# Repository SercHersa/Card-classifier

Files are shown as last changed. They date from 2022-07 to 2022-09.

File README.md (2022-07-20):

# Card-classifier

En este repositorio, se subirá todo lo referente al desarrollo del proyecto de un clasificador de tarjetas, el cual es un robot movil que llega a un stock de tarjetas y mediante tecnología RFID, detecta dónde deberá llevar la tarjeta y mediante la programación de cirtas trayectorias, la depositará en diferentes estantes.

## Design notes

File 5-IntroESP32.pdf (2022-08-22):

# Introducción a la Ingeniería

## Introducción a Arduino y la placa ESP32

### Objetivo

Familiarizarse con el ambiente de programación de Arduino Aprender a interconectar entradas y salidas a la placa ESP32

### Materiales

Un controlador ESP32 y cable USB para conectarlo a la PC El IDE Arduino con la librería para ESP32
Una tarjeta protoboard,
Tres leds, cables y resistencias

### Introducción

Arduino es probablemente la plataforma de hardware abierto más popular para desarrollo y prototipado rápido de proyectos de sistemas digitales. Ha logrado conformar una amplísima comunidad de desarrolladores que comparten las especificaciones y el código de sus proyectos.

Las tarjetas Arduino tienen una serie de interfaces entrada y salida (E/S) analógicas y digitales que pueden ser programadas para monitorear (con ayuda de sensores) o interactuar (con ayuda de actuadores) con su entorno.

Hay una gran variedad de sensores (por ejemplo, de temperatura, humedad, iluminación, sonido, contaminantes, nutrientes, posicionamiento, velocidad, lector RFID, …) y actuadores (por ejemplo, LEDs, zumbadores, relevadores, acopladores, pinzas, servo motores, …) que pueden conectarse a una placa Arduino a través de sus interfaces programables E/S.

Arduino cuenta con un ambiente de desarrollo integrado (IDE, Integrated Development Environment) para programar las acciones que se desean configurar en la placa. Los programas (llamados sketch) escritos en el IDE se descargan a la placa a través de la interfaz USB.

La popularidad de Arduino es tan grande, que su ambiente de programación se ha vuelto un estándar de facto en la comunidad de hardware abierto. Es por ello que utilizaremos el IDE de Arduino en nuestro primer proyecto.

Si bien las tarjetas Arduino son sumamente populares, no son las únicas. En los últimos años han aparecido muchas otras placas para desarrollo de sistemas digitales por lo que hoy tenemos una amplia gama de opciones.

Entre ellas está el microcontrolador ESP32 de Esspresif Systems, un dispositivo sumamente poderoso y versátil. Al igual que las placas Arduino, puede recibir y enviar datos analógicos y digitales, procesar datos e interactuar con usuarios a través de la computadora personal. Además, el módulo ESP32 tiene integrado un chip Bluetooth y uno WiFi lo que le permite conectarse a Internet.

En nuestro primer proyecto, el Robot que utilizará está controlado por una tarjeta Arduino y el lector RFID, que programará usted, está controlado por una tarjeta ESP32.

## Desarrollo

### 1. Instalación del IDE y de las librerías

El IDE permite expresar un programa (un sketch) en un lenguaje muy parecido a C que se compila en el lenguaje de máquina del micro-controlador de la placa. Descargue el IDE de la siguiente dirección: https://www.arduino.cc/en/Main/Software.

Para poder programar el módulo ESP32 desde el IDE de Arduino, es necesario configurar el IDE y cargar algunas librerías. Para ello, sigas las instrucciones en esta liga: https://randomnerdtutorials.com/installing-the-esp32-board-in-arduino-ide-windows-instructions/. NO SE DESESPERE. ESTO TOMARÁ ALGÚN TIEMPO. (Nota: No es necesario que (https://randomnerdtutorials.com/installing-the-esp32-board-in-arduino-ide-windows-instructions/) haga la validación buscando redes WiFi).

### 2. Verificación

Como se señala en la guía anterior, una vez configurado el IDE, deberá seleccionar la placa ESP32 y el puerto COM en la que está conectada. La placa que se le entregó para este proyecto es DOIT

ESP DEVKIT V1 .

1. Conecte el módulo a su PC a través del cable USB. Se debió haber encendido un led rojo indicando que la placa está energizada.
2. En el IDE de Arduino, en el menú Herramientas , seleccione la placa

ESP32 Arduino/DOIT ESP DEVKIT V1
3. En el mismo menú seleccione el puerto al que está conectada la placa
4. En el menú Archivo/Ejemplos/ seleccione el sketch 01.Basics/Blink
5. Compílelo dando clic en el ícono con una paloma. Si no tiene errores, cárguelo a la placa dando clic en la flecha a la derecha:

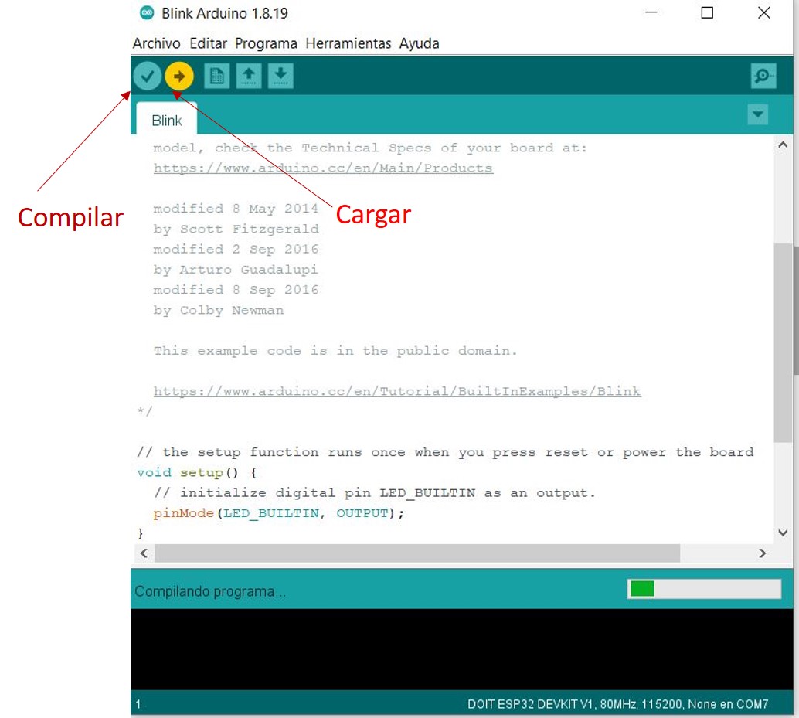
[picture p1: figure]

Figura 1. Compilar y cargar un sketch en el IDE de Arduino

6. Si todo está correcto, podrá ver un led azul parpadeando

EJERCICIO 1. ( 1 Punto). Muestre el led parpadeando al profesor

7. Ahora modifique el sketch para que el led se mantenga encendido un segundo y apagado medio segundo.

EJERCICIO 2. (2 Puntos). Muestre al profesor el led parpadeando con las modificaciones solicitadas

EJERCICIO 3. (1 Punto). Analice y describa brevemente qué hace el código.

### 3. Conectar y manipular un led externo

En esta sección nos vamos a familiarizar con la conexión de componentes electrónicos en una tarjeta protoboard, (también conocidas como Breadboard) como la mostrada en la Figura 2:

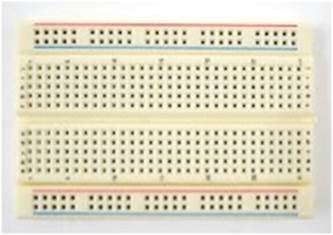
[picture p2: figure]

Figura 2. Tarjeta Protoboard

Las tarjetas protoboard (placa de pruebas) permiten crear rápidamente prototipos de circuitos electrónicos. Son tablas con orificios que se encuentran interconectados entre sí internamente. En la Figura 2, los orificios paralelos a las líneas rojas y azules están interconectados y se usan típicamente para transportar señales de voltaje y de tierra. Los orificios verticales (las columnas) entre las muescas de la tarjeta (por ejemplo, los orificios 12A a 12E), también están interconectados entre sí.

Vamos a colocar un LED en la tarjeta protoboard que encenderemos y apagaremos desde el ESP32. Para ello, el "cátodo" del LED, que se reconoce por ser la pata más corta y tener una muesca plana en el plástico que lo recubre, se conecta a tierra. El "anodo" se conecta a una pata digital de Entrada/Salida (E/S) de la placa ESP32 a través de un resistor de 1kOhm (en realidad, el valor no importa demasiado; resistencias más grandes,disminuirán la corriente y con ello, la intensidad de luminosidad del led).

Existen muchos modelos ESP32. El que se le entregó tiene 30 pines. La distribución de pines en ese modelo es la que se muestra en la figura 3:

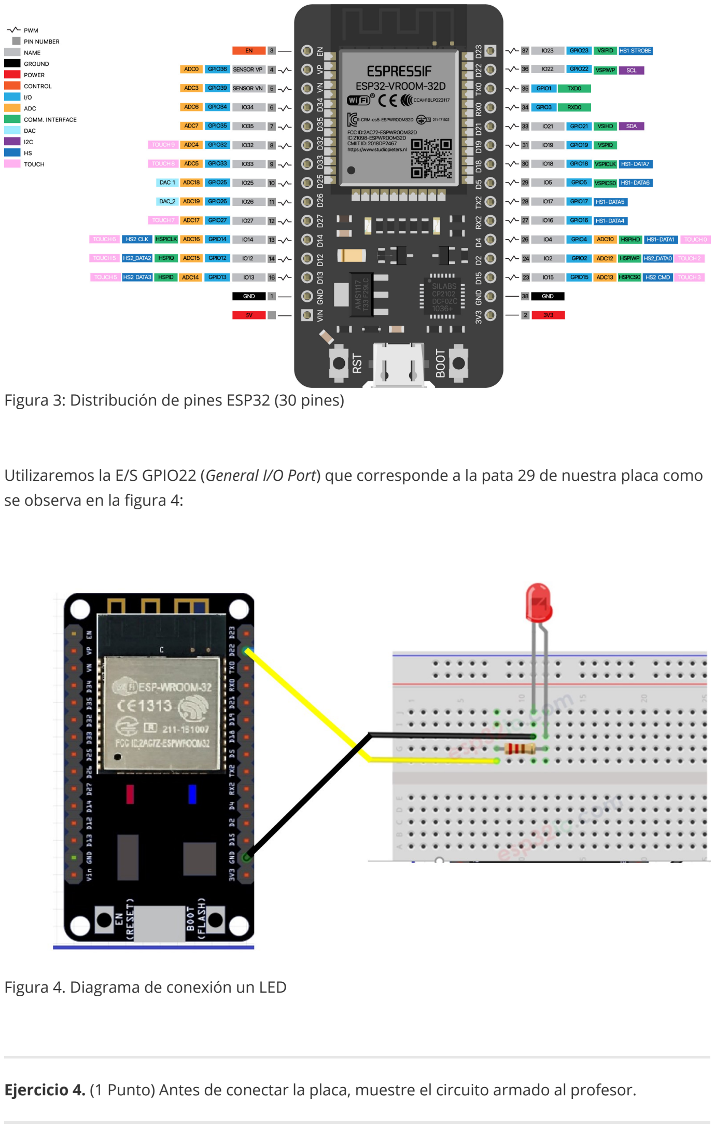
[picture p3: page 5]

Figura 3: Distribución de pines ESP32 (30 pines)

Utilizaremos la E/S GPIO22 (General I/O Port) que corresponde a la pata 29 de nuestra placa como se observa en la figura 4:

Figura 4. Diagrama de conexión un LED

Ejercicio 4. (1 Punto) Antes de conectar la placa, muestre el circuito armado al profesor.

Guarde el código del sketch de parpadeo con un nuevo nombre, por ejemplo, "LedExterno". Vamos a modificar el código para que cuando el LED de la placa esté encendido, el LED en el protoboard se apague y viceversa. Los segmentos de código que necesitará son los siguientes:

EJERICIO5. (2 Puntos). Modifique el código, cárguelo a la placa ESP32 y muestre el circuito funcionando al profesor.

EJERICIO 6. (3 Puntos). Muy bien. Ahora deberá conectar dos LEDs adicionales en los pines de E/S que usted desee. No se olvide de conectar los LEDs con resistores a los pines. Escriba un sketch para que los tres LEDS se alternen en el encendido: LED1 un segundo, LED2 un segundo, LED3 un segundo.

Muestre el sistema funcionando a su profesor

// Antes de setup
#define LED_PROTOBOARD 22 // GPIO que se utilizará para iluminar LED externo

// En setup
pinMode(LED_PROTOBOARD, OUTPUT); // GPIO22 como salida digital

// En loop
digitalWrite(LED_PROTOBOARD, HIGH); ...
digitalWrite(LED_PROTOBOARD, LOW); ...

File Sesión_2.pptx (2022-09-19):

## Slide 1

Clasificador de
tarjetas

M.I. Sergio Hernández Sánchez
sergio.hernandez.sanchez@itam.mx

1

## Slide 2

Salidas Digitales

M.I. Sergio Hernández Sánchez

2

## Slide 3

ESP32 DEVKIT v1 - PINOUT

GPIO = General Purpose Input/Output

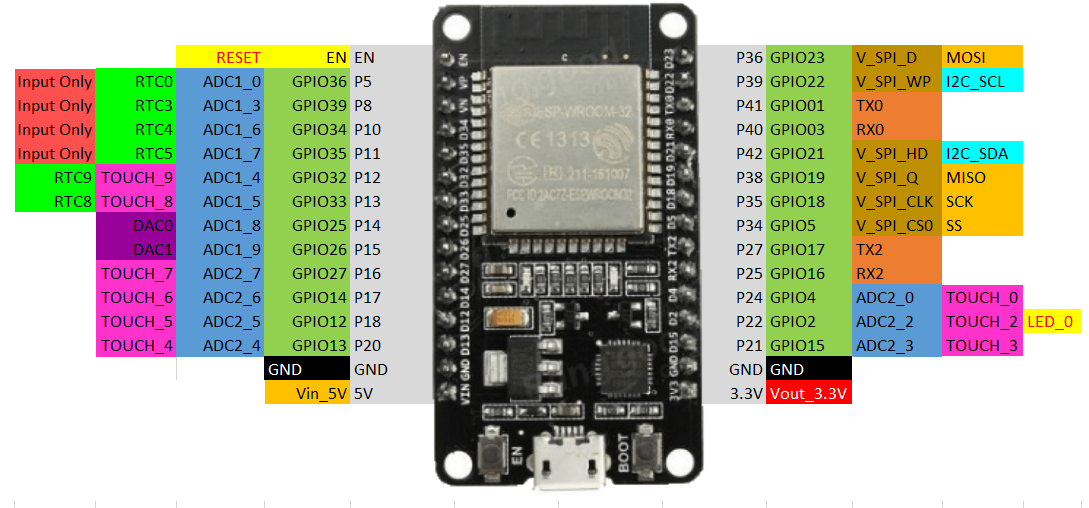
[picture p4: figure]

M.I. Sergio Hernández Sánchez

3

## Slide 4

Salidas digitales

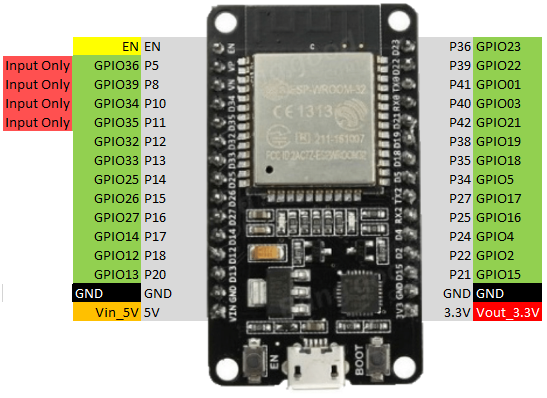
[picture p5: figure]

M.I. Sergio Hernández Sánchez

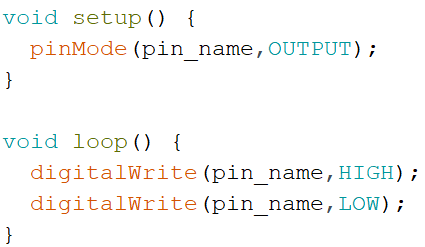
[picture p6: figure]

4

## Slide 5

Comunicación Serial

M.I. Sergio Hernández Sánchez

5

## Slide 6

Comunicación Serial

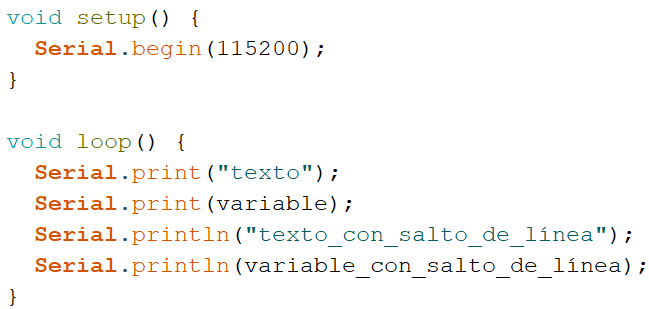
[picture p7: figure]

M.I. Sergio Hernández Sánchez

6

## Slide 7

Entradas digitales

M.I. Sergio Hernández Sánchez

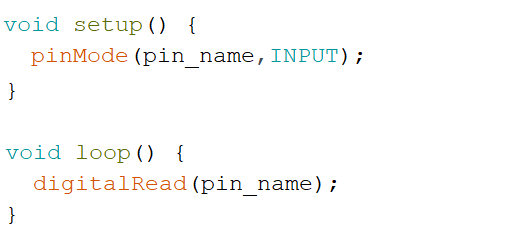
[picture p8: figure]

7

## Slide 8

Entradas digitales

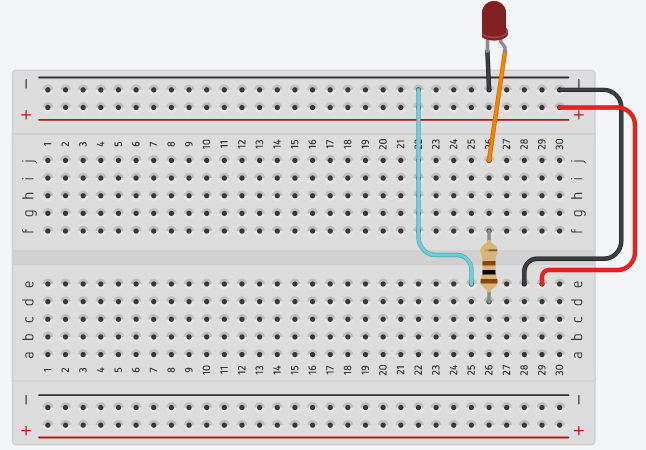
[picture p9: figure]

M.I. Sergio Hernández Sánchez

8

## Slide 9

Entradas digitales

M.I. Sergio Hernández Sánchez

9

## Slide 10

Entradas digitales

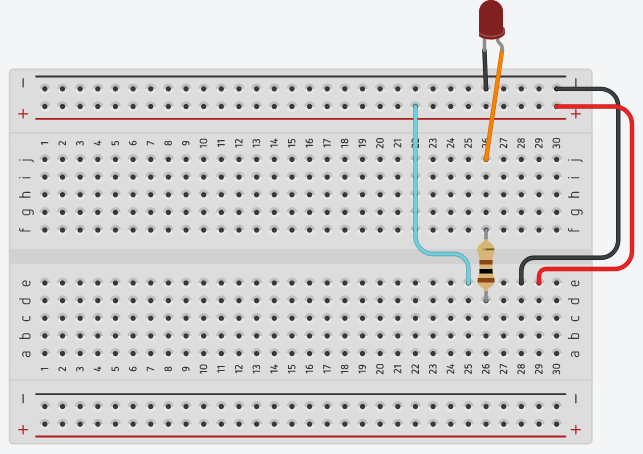
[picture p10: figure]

M.I. Sergio Hernández Sánchez

10

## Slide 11

Entradas digitales

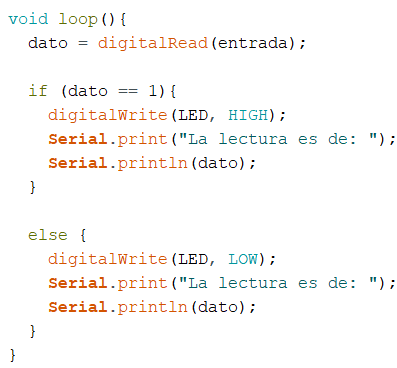
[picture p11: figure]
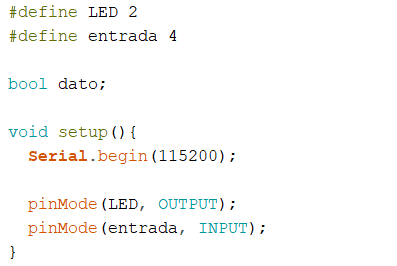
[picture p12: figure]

M.I. Sergio Hernández Sánchez

11

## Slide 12

Funciones

M.I. Sergio Hernández Sánchez

12

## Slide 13

Funciones

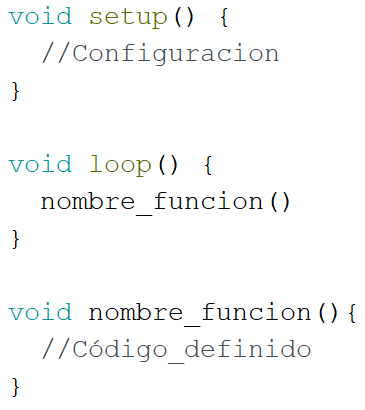
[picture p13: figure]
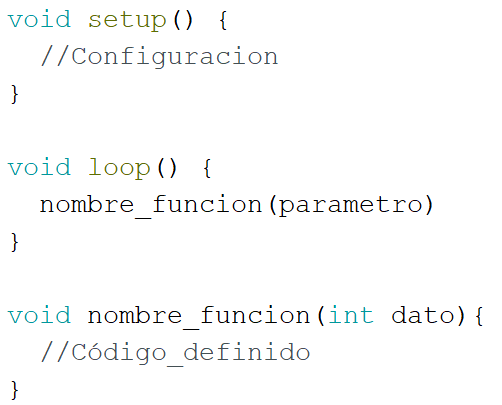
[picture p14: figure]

M.I. Sergio Hernández Sánchez

13

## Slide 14

Codificador binario

M.I. Sergio Hernández Sánchez

14

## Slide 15

Circuito codificación

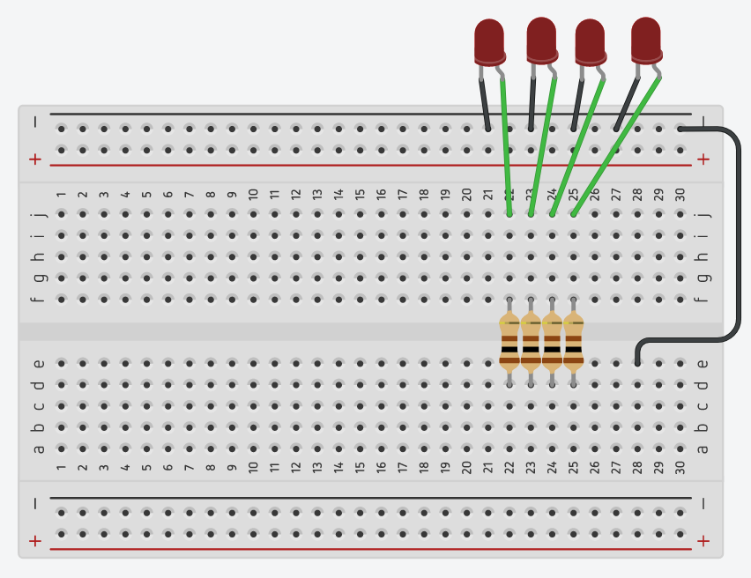
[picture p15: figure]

M.I. Sergio Hernández Sánchez

15

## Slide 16

Reto

Hacer un contador binario de 0 a 15, incrementando la cuenta de uno en uno cada segundo y se reinicie para volver a hacer la cuenta. Este incremento se debe mostrar con cuatro leds y a su vez, mostrarse en el monitor serial.

M.I. Sergio Hernández Sánchez

16

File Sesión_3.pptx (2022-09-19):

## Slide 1

Clasificador de
tarjetas

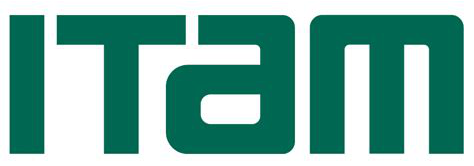
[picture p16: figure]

M.I. Sergio Hernández Sánchez
sergio.hernandez.sanchez@itam.mx

1

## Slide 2

Lector RFID

M.I. Sergio Hernández Sánchez

2

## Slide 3

Lector RFID

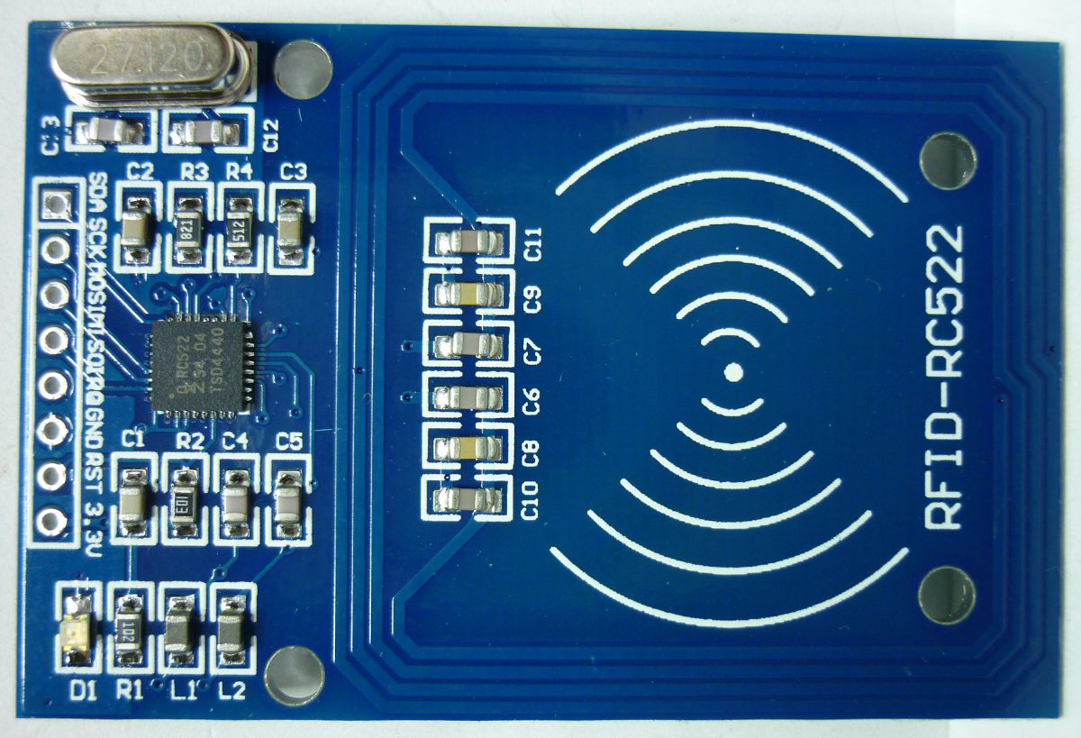
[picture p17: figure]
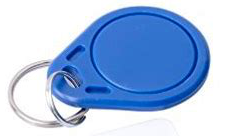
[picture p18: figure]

M.I. Sergio Hernández Sánchez

3

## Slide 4

Conexión

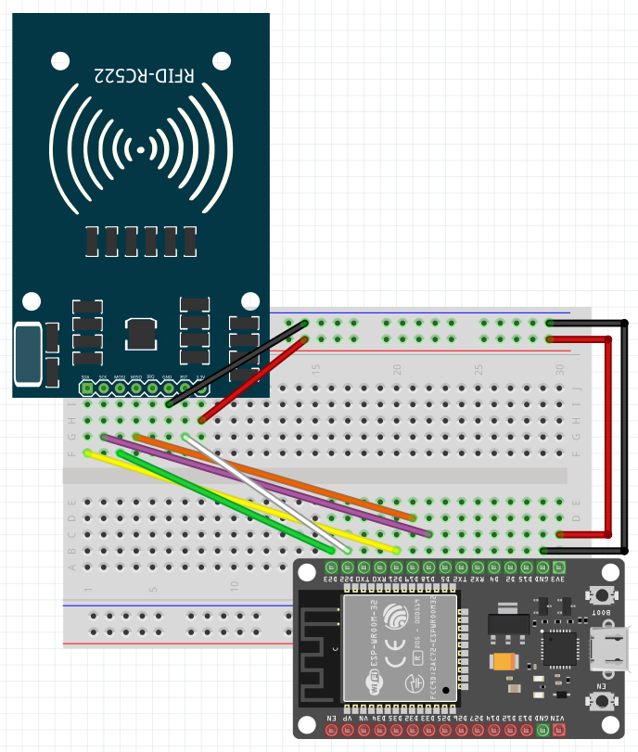
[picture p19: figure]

M.I. Sergio Hernández Sánchez

4

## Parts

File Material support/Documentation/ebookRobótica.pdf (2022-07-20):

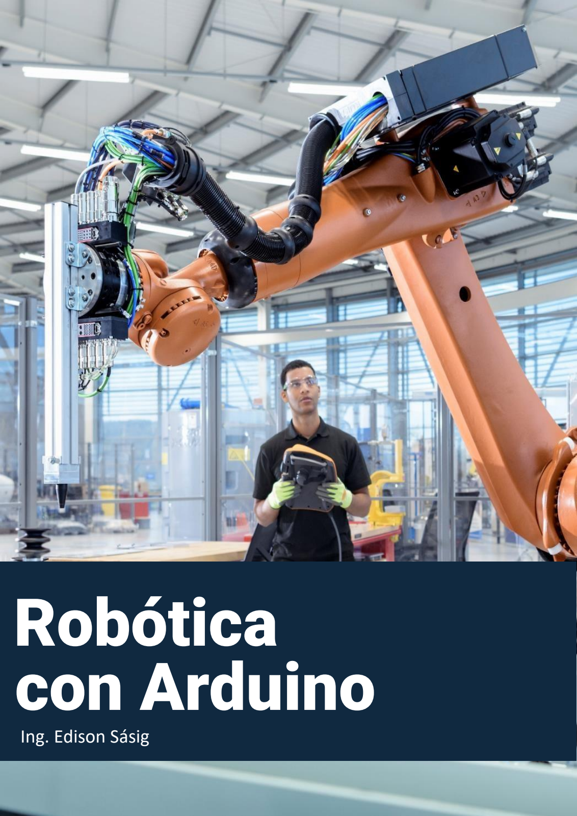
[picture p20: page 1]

# Ing. Edison Sásig

# Robótica con Arduino

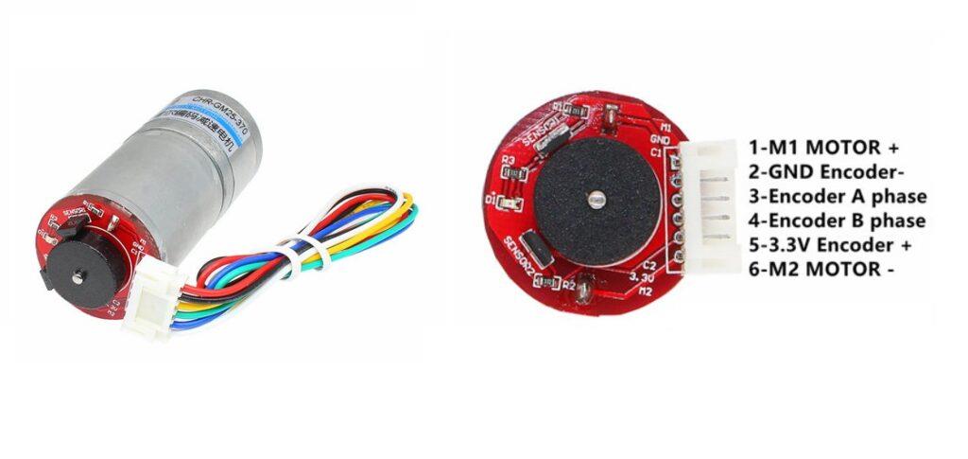
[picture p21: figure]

1 | Ing. Edison Sásig

# Encoder de cuadratura para Robótica

# ¿Qué es un encoder de cuadratura?

Un encoder de cuadratura es un tipo de encoder rotativo incremental que tiene la capacidad de indicar tanto la posición como la velocidad y la dirección del movimiento del eje del motor.

En este apartado vamos a revisar encoders con sensores magnéticos de efecto Hall. A diferencia de los encoders ópticos, los sensores hall al ser magnéticos pueden trabajar en entornos extremos (temperatura, salpicadura de fluidos, grasas, etc) y polvorientos; no hará falta mantenimiento de limpieza.

Debido a estas características los encoder en cuadratura son muy útiles para las siguientes aplicaciones en robótica:

- Robots móviles tipo Uniciclo
- Robots móviles tipo omnidireccional (Mecanum, 3 ruedas)
- Robots móviles tipo Car-Like
- Brazos robóticos
- Robot tipo péndulo
- Robot rueda esférica y mucho más.

Este encoder tiene dos sensores de efecto Hall que generan dos señales de pulsos digitales desfasada en 90º eléctricos o en cuadratura gracias a un disco magnético giratorio, montado en el eje trasero del motor. A estas señales de salida, se les llama comúnmente A y B. Estos dos sensores se van activando y desactivando en una secuencia que nos permite saber la dirección y el número de desplazamientos que han ocurrido en el encoder.

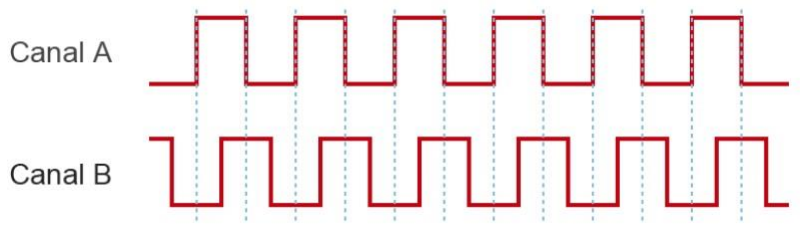
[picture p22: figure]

# Sentido de giro

Para la determinar el sentido de giro (signo), se toman como referencia el desfasamiento que existe entre las señales AB. El hecho de trabajar con dos canales, nos lleva a tener 4 estados, estos mismos son la combinación de A y B.

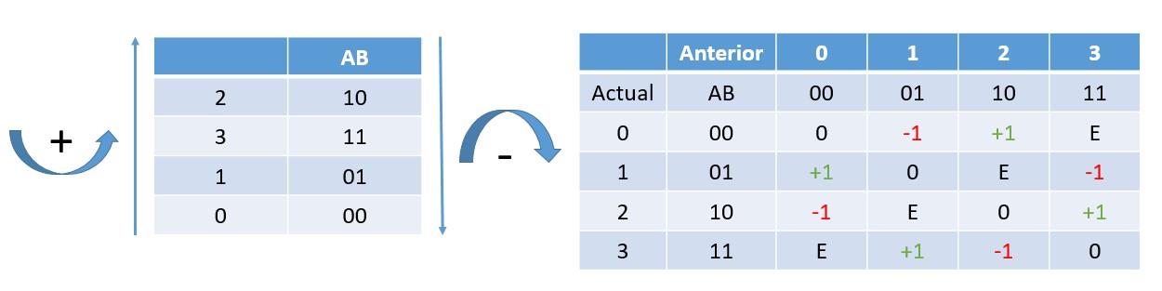
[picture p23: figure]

Si asumimos la salida A como el bit más significativo y la salida B como el bit menos significativo, en la tabla de verdad podemos saber la dirección de giro, si comparamos el estado actual con el estado anterior.

Además, en la figura también se muestra una matriz de incrementos donde podemos comparar el estado anterior con el actual y saber cómo fue el movimiento. Por ejemplo, si el estado anterior fue 01 y el estado actual del encoder es 11 podemos saber que el motor está girando en sentido anti-horario (+). Esta matriz es muy útil para saber en pocos pasos que ocurre con el encoder. También nos puede servir para detectar errores de nuestra señal o del encoder. Ya que hay 4 combinaciones que no pueden aparecer en nuestra señal, como por ejemplo la combinación (11,00), marcada con una E en la matriz.

# Resolución

La resolución de un encoder es una medida en pulsos por revolución (PPR), es decir el número de conteo (cuentas) que genera el encoder en cada vuelta. En el caso de los motores Chihai Motor CHR-GM25-370 de 140RPM a 12v, el encoder incremental de cuadratura emite 11 cuentas por revolución del eje del motor, que corresponde a 495 cuentas por revolución del eje de salida de la caja de reductora (Holzer resolution).

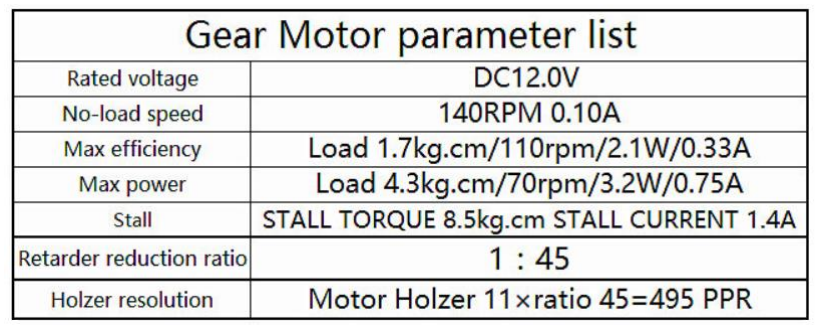
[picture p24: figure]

Respecto a la precisión, tenemos más de una opción.

- Precisión simple, registrando un único flanco (subida o bajada) en un único canal.
- Precisión doble, registrando ambos flancos en un único canal.
- Precisión cuádruple, registrando ambos flancos en ambos canales.

# Resolución para una precisión cuádruple

Para aplicaciones de robótica se utiliza la precisión cuádruple, esta precisión es la que permite detectar el sentido de giro del eje del motor. Por lo tanto, la resolución del encoder para una precisión cuádruple (R) se calcula de manera diferente al Holzer resolution.

# R mH s r = × ×

Donde:

R :
Es la resolución del encoder para una precisión cuádruple.

mH :
Es el número de cuentas por revolución del eje del motor (Motor Holzer). En nuestro

caso 11.

s:
Es el número de estados generado por los canales AB. En nuestro caso 4.

r:
Es la relación de reducción de la caja reductora (ratio). En nuestro caso 45 cuentas por

revolución.

Por lo tanto,
R = | × × | = 11 4 45 1980

# Sentido de giro en Arduino

En base a la tabla anterior se debe crear un código que permita comparar el estado anterior y el estado actual de los pines C1 (canal A) y C2 (canal B) del encoder.

En primer lugar, se debe detectar los flancos de subida y bajada de ambos canales AB. Para esta tarea lo más recomendable es usar interrupciones. Entonces, definimos los pines y las variables que se van a utilizar, configuramos los pines como entradas y activamos las interrupciones para detectar ambos flancos.

const int | C1 = 3; | // Entrada de la señal A del encoder.
const int | C2 = 2; | // Entrada de la señal B del encoder.

void setup()
{

pinMode(C1, INPUT);
pinMode(C2, INPUT);

attachInterrupt(digitalPinToInterrupt(C1), encoder, CHANGE); attachInterrupt(digitalPinToInterrupt(C2), encoder, CHANGE);

}

En la función encoder vamos a comparar el estado anterior y actual e incrementar o decrementar un contador según la tabla. Para esta tarea, vamos a leer un puerto completo que dependiendo en donde se encuentre conectado los pines puede variar.

Los chips utilizados en la placa Arduino (ATmega8 y ATmega168) tienen tres puertos:

- B (pines digitales de 8 a 13) PINB
- C (pines de entrada analógica) PINC
- D (pines digitales de 0 a 7) PIND

En este caso estamos utilizando los pines 2 y 3 es decir el puerto D, por lo tanto, para leer el puerto completo usaremos PIND.

Adicionalmente, debemos filtrar solo los pines de interés este caso el 2 y 3. Entonces considerando que los puertos de Arduino (ATmega8 y ATmega168) son de 8 bits se puede aplicar una operación and entre el valor de PIND y 00001100 (12 DECIMAL).

Entonces en base a tabla debemos hacer la comparación sin olvidar que los valores de la tabla también cambian en base a la conexión de los pines, es decir, si hay un flanco en el canal A (pin 3) y nada en el canal B (pin 2) el valor binario es 10 (2 DECIMAL) se debe cambiar a 00001000 (8 DECIMAL) y así en todas las combinaciones 00, 01 y 11.

0 0 0 0 | 1 1 | 0 0
7 6 5 4 | 3 2 | 1 0
0 0 0 0 | 1 0 | 0 0
7 6 5 4 | 3 2 | 1 0

// Encoder precisión cuádruple. void encoder(void)
{

ant=act;
act=PIND & 12;
if(ant==0 | && act== 4) | n++;
if(ant==4 | && act==12) | n++;
if(ant==8 | && act== 0) | n++;
if(ant==12 && act== 8) | n++;
if(ant==0 && act==8) | n--;
if(ant==4 && act==0) | n--;
if(ant==8 && act==12) n--; if(ant==12 && act==4) n--;

}

Entonces, si cargamos el siguiente sketch en Arduino al dar una vuelta completa al eje del motor se debe mostrar en el monitor serial el valor de la resolución del encoder para una precisión cuádruple

R
. Para este caso

R =1980 .

const int | C1 = 3; | // Entrada de la señal A del encoder.
const int | C2 = 2; | // Entrada de la señal B del encoder.

volatile int n = 0;
volatile byte ant | = 0;
volatile byte act | = 0;
unsigned long lastTime = 0; | // Tiempo anterior
unsigned long sampleTime = 100; | // Tiempo de muestreo

void setup()
{
Serial.begin(9600);

pinMode(C1, INPUT);
pinMode(C2, INPUT);

attachInterrupt(digitalPinToInterrupt(C1), encoder, CHANGE); attachInterrupt(digitalPinToInterrupt(C2), encoder, CHANGE);

Serial.println("Numero de conteos");

}

void loop() {
if (millis() - lastTime >= sampleTime)
{ // Se actualiza cada sampleTime (milisegundos) lastTime = millis();
Serial.print("Count: ");Serial.println(n); }
}

// Encoder precisión cuádruple. void encoder(void)
{

ant=act;
act=PIND & 12;
if(ant==0 | && act== 4) | n++;
if(ant==4 | && act==12) | n++;
if(ant==8 | && act== 0) | n++;
if(ant==12 && act== 8) | n++;
if(ant==0 && act==8) | n--;
if(ant==4 && act==0) | n--;
if(ant==8 && act==12) n--; if(ant==12 && act==4) n--;

}

El código anterior se aplica para un solo motor. Sin embargo, en robótica el número de motores puede ser mucho mayor dependiendo de la aplicación. Entonces vamos a necesitar pines adicionales con interrupciones, y como saben Arduino (ATmega8 y ATmega168) dispone de dos interrupciones externas, por lo cual debemos usar otro Arduino como el MEGA o incluso un ESP32 que tienes muchas características adicionales al tradicional Arduino.

Sin embargo, el Arduino tradicional dispone de interrupciones especiales llamadas PINCHANGE INTERRUPTIONS, las cuales se pueden utilizar en todos los pines incluso en las entradas analógicas, pero son un poco complejas de administrar, sin embargo, gracias la librería PinChangeInterrupt.h podemos utilizar estas interrupciones de la misma manera que una interrupción normal.

En el siguiente ejemplo se ha empleado las interrupciones en el puerto C y en los pines A4 (canal A) y A5 (canal B).

#include "PinChangeInterrupt.h"

const int C1 = A5;
const int C2 = A4;
volatile int n = 0;
volatile int ant | = 0;
volatile int act | = 0;

unsigned long lastTime, sampleTime = 100;

void setup() {

Serial.begin(9600);

pinMode(C1, INPUT);
pinMode(C2, INPUT);

attachPinChangeInterrupt(digitalPinToPinChangeInterrupt(C1), encoder, CHANGE);
attachPinChangeInterrupt(digitalPinToPinChangeInterrupt(C2), encoder, CHANGE);

lastTime = millis();

}

void loop() {
if(millis()-lastTime >= sampleTime) {
lastTime = millis();
Serial.println(n);
}
}

void encoder(void)
{

ant=act;
act=PINC & 48;
if(ant==0 | && act==16) | n++;
if(ant==16 && act==48) | n++;
if(ant==32 && act== 0) | n++;
if(ant==48 && act==32) | n++;
if(ant==0 | && act==32) | n--;
if(ant==16 && act== 0) | n--;
if(ant==32 && act==48) | n--;
if(ant==48 && act==16) | n--;

}

Recuerda que para leer todo el puerto C se debe usar PINC y también se debe realizar la conversión en decimal de los estados de los pines A4 y A5.

# Posición en grados

Para medir la posición relativa del eje del motor, vamos a utilizar la siguiente fórmula.

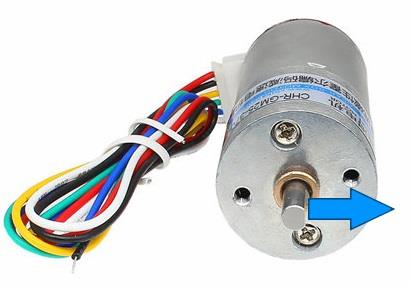
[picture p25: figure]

8 | Ing. Edison Sásig n 360 P
R

×
=

Donde:

P :
Es la posición relativa en grados.

n :
Es el número de cuentas generadas.

R :
Es la resolución del encoder para una precisión cuádruple. En nuestro caso 1980

cuentas por revolución.

# Posición en grados en Arduino

Una vez verificado el código anterior es muy fácil obtener la posición, velocidad y sentido de giro del eje del motor, simplemente hay que aplicar las fórmulas.

const int | C1 = 3; | // Entrada de la señal A del encoder.
const int | C2 = 2; | // Entrada de la señal B del encoder.

volatile int n = 0;
volatile byte ant | = 0;
volatile byte act | = 0;

double P = 0.0;
unsigned long lastTime = 0; | // Tiempo anterior
unsigned long sampleTime = 100; | // Tiempo de muestreo

unsigned int R = 1980; // Resolucion del encoder R = mH*s*r

void setup()
{
Serial.begin(9600)

pinMode(C1, INPUT);
pinMode(C2, INPUT);

attachInterrupt(digitalPinToInterrupt(C1), encoder, CHANGE); attachInterrupt(digitalPinToInterrupt(C2), encoder, CHANGE);

Serial.println("Posicion en grados");

}

void loop() {
posValue();
}

void posValue(void)

{
if (millis() - lastTime >= sampleTime)
{ // Se actualiza cada sampleTime (milisegundos) lastTime = millis();
P = (n*360.0)/R;
Serial.print("Posicion: ");Serial.println(P); }

}

// Encoder precisión cuádruple. void encoder(void)
{

ant=act;
act=PIND & 12;
if(ant==0 | && act== 4) | n++;
if(ant==4 | && act==12) | n++;
if(ant==8 | && act== 0) | n++;
if(ant==12 && act== 8) | n++;
if(ant==0 && act==8) | n--;
if(ant==4 && act==0) | n--;
if(ant==8 && act==12) n--; if(ant==12 && act==4) n--;

}

# Velocidad angular en RPM

Para medir las revoluciones por minuto, vamos a utilizar la siguiente fórmula.
n 60 N
tR

×
=
×

Donde:

N :
Es la velocidad de rotación en Revoluciones Por Minuto (RPM).

n :
Es el número de conteo generado en determinado tiempo

t

t :
Es el tiempo de generación de los pulsos en segundos (s).

R :
Es la resolución del encoder para una precisión cuádruple. En nuestro caso 1980 cuentas

por revolución.

# Velocidad angular en RPM en Arduino

En este caso debemos obtener el número de cuentas en un determinado tiempo de muestreo y aplicar la fórmula. Recuerde que el tiempo

t
es en segundos, sin embargo, en microcontroladores se trabaja en el orden de los microsegundos o milisegundos.

Para trabajar en milisegundos se debe hacer la siguiente conversión 1s = 1000ms y aplicarlo a la fórmula de la siguiente manera.
n 60 1000 N
tR

× ×
=
| ×

if (millis() - lastTime >= sampleTime)
{// Se actualiza cada tiempo de muestreo
N =(n*60.0*1000.0)/((millis()-lastTime)*R);// Velocidad en RPM lastTime = millis(); // Almacenamos el tiempo actual.
n = 0; // Inicializamos los pulsos.
}

Recuerde que cada tiempo de muestreo debemos resetear el valor del contador para obtener una nueva lectura en el siguiente instante de muestreo. Entonces agregando el control de velocidad el código es el siguiente.

String inputString = "";
bool stringComplete = false;
const byte | C1 = 3; | // Entrada de la señal A del encoder
(Cable amarillo).
const byte | C2 = 2; | // Entrada de la señal B del encoder
(Cable verde).
const byte | in1 = 6;
const byte | in2 = 7;
const byte | ena = 10;

volatile int n = 0;
volatile byte ant | = 0;
volatile byte act | = 0;
double N = 0.0; | // Revoluciones por minuto calculadas.
int Cv =0; // Variable de control (pwm)
unsigned long lastTime = 0; | // Tiempo anterior
unsigned long sampleTime = 100; | // Tiempo de muestreo

unsigned int R = 1980; // Número de muescas que tiene el disco del encoder.

void setup()
{

Serial.begin(9600);

pinMode(C1, INPUT);
pinMode(C2, INPUT);

pinMode(in1, OUTPUT);
pinMode(in2, OUTPUT);

digitalWrite(in1, false);
digitalWrite(in2, false);

analogWrite(ena,Cv);

attachInterrupt(digitalPinToInterrupt(C1), encoder, CHANGE); attachInterrupt(digitalPinToInterrupt(C2), encoder, CHANGE);

Serial.println("Velocidad RPM");
}

void loop() {
if (stringComplete)
{

Cv=(double)inputString.toInt();

inputString = "";
stringComplete = false;
}

computeRpm();

}

void serialEvent() {
while (Serial.available()) {
char inChar = (char)Serial.read(); inputString += inChar;
if (inChar == '\n') {
stringComplete = true;
}
}
}

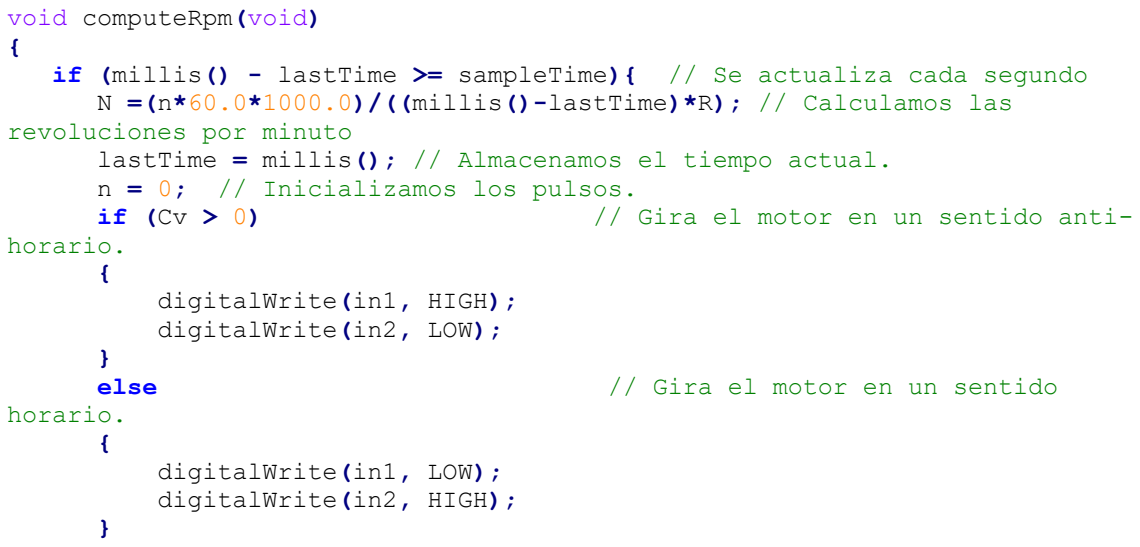
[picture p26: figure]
void computeRpm(void) {; revoluciones por minuto; // Inicializamos los pulsos.; horario. {; digitalWrite(in1, HIGH); digitalWrite(in2, LOW);; else; // Gira el motor en un sentido; digitalWrite(in1, LOW); digitalWrite(in2, HIGH);

if (millis() - lastTime >= sampleTime){ // Se actualiza cada segundo N =(n*60.0*1000.0)/((millis()-lastTime)*R); // Calculamos las

lastTime = millis(); // Almacenamos el tiempo actual.

if (Cv > 0) | // Gira el motor en un sentido anti-

analogWrite(ena,abs(Cv)); | // Aplica señal de control (pwm).
Serial.print("RPM: ");Serial.println(R);
}

}

// Encoder precisión cuádruple. void encoder(void)
{

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

}

# Velocidad angular en por segundo (rad/s)

Con las revoluciones por minuto RPM se puede encontrar la velocidad angular en rad/s. Una revolución equivale a

2π
radianes y 1 minuto equivale a 60 segundos. Por la tanto, la velocidad angular se puede calcular de la siguiente manera.

2
60

N
w

π ×
=

Donde:

w:
Es la velocidad de rotación en radianes por segundo (rad/s).

N :
Es la velocidad de rotación en Revoluciones Por Minuto (RPM).

Otra forma de calcular la velocidad angular en función del número de cuentas es de la

siguiente manera.
2 n
w
tR

π ×
=
×

Donde:

13 | Ing. Edison Sásig w:
Es la velocidad de rotación en radianes por segundo (rad/s).

n :
Es el número de conteo generado en determinado tiempo

t

t :
Es el tiempo de generación de los pulsos en segundos (s).

R :
Es la resolución del encoder para una precisión cuádruple. En nuestro caso 1980 cuentas

por revolución.

# Velocidad angular en Arduino

Al igual que en el cálculo de la velocidad en RPM, en el cálculo de la velocidad angular en rad/s se debe aplicar la fórmula con el respectivo cambio del tiempo en ms.
2 1000 n
w
| tR
π × | ×
=
×

Donde

π = 3.1416

if (millis() - lastTime >= sampleTime)
{// Se actualiza cada tiempo de muestreo
w =(2*pi*1000.0*n)/((millis()-lastTime)*R);// Velocidad angular lastTime = millis(); // Almacenamos el tiempo actual.
n = 0; // Inicializamos los pulsos.
}

Sin embargo, para optimizar el código vamos a considerar

2 1000
R

π ×
como una constante.

Si

π = 3.1416, R =1980
, entonces, la constante es

constValue = 3.1733

if (millis() - lastTime >= sampleTime)
{// Se actualiza cada tiempo de muestreo
w =(constValue*n)/(millis()-lastTime); // Velocidad angular rad/s lastTime = millis(); // Almacenamos el tiempo actual.
n = 0; // Inicializamos los pulsos.
}

# Velocidad lineal en metros por segundo (m/s)

Para calcular la velocidad lineal en metros por segundo solamente se tiene que multiplicar la

velocidad angular por el radio de la llanta conectada al eje de salida de la caja reductora.

wheel u r | w = | ×

Donde:

14 | Ing. Edison Sásig u :
Es la velocidad lineal en metros por segundo m/s.

w:
Es la velocidad de rotación en radianes por segundo (rad/s).

: wheel r
Es el radio de la rueda en metros (m).

Otra manera de calcular la velocidad lineal en función del número de cuentas y el diámetro

de la llanta es la siguiente.

wheel d | n
u
tR

×× π
=
×

Donde:

u :
Es la velocidad lineal en metros por segundo m/s.

: wheel d
Es el diámetro de la rueda en metros (m).

n :
Es el número de conteo generado en determinado tiempo

t

t :
Es el tiempo de generación de los pulsos en segundos (s).

R :
Es la resolución del encoder para una precisión cuádruple. En nuestro caso 1980

cuentas por revolución.

# Velocidad lineal en Arduino

De la misma manera vamos a optimizar el código considerando

### 1000 wheel d

R

×× π
como

constante.

Si

0.067 wheel d | = | , R =1980
, entonces, la constante es

constValue = 0.1063

if (millis() - lastTime >= sampleTime)
{// Se actualiza cada tiempo de muestreo
u =(constValue*n)/(millis()-lastTime); // Velocidad lineal m/s lastTime = millis(); // Almacenamos el tiempo actual.
n = 0; // Inicializamos lo``s pulsos.
}

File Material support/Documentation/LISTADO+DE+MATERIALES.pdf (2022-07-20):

ROBOT MÓVIL AUTÓNOMO TIPO DIFERENCIAL (https://roboticoss.com/curso/robotica-con-python-y-arduino-robot-movil-diferencial/) | PÁG 1

LISTADO DE MATERIALES, HERRAMIENTAS, DISPOSITIVOS Y SOFTWARE A EMPLEAR EN EL CURSO

CURSO: | ROBOT MÓVIL AUTÓNOMO TIPO DIFERENCIAL
1. MATERIALES A EMPLEAR EN LA CONSTRUCCIÓN DEL ROBOT
CANTIDAD | MATERIAL | DESCRIPCIÓN | REFERENCIA
1 | Arduino Nano y cable usb | Es el cerebro del robot, los códigos son compatibles solo con esta versión Arduino.
1 | Módulo bluetooh HC-05 | Utilizado para la comunicación inalámbrica con Python y Arduino.
1 | Módulo L298N | Driver para el control de los motores de corriente directa.

ROBOT MÓVIL AUTÓNOMO TIPO DIFERENCIAL (https://roboticoss.com/curso/robotica-con-python-y-arduino-robot-movil-diferencial/) | PÁG 2

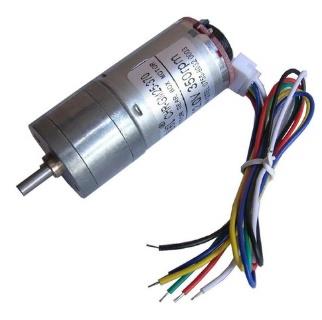
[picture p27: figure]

2

Motores con encoder de

cuadratura

Motor Chihai de 140RPM a 12V,

sin embargo, puede usar versiones

similares de 120 a 350 RPM de 12

Voltios, recomiendo marca Chihai

y Pololu


1 | Batería LiPo 3S 1000mAh

La Batería LiPo 3S está constituida

por 3 celdas, su voltaje es de 11.1V

y una corriente de 1000mAh, es

utilizado para suministrar la

energía al robot (Duración

aproximada 1 Hora). Si desea que

dure más tiempo comprar de mas

mah.


1

Cargador de batería de 2S y

3S

Cargador de batería Li-Po con

enchufe de pared de entrada de AC,

voltaje de entrada: 100-240 VAC,

carga de energía: 18W (máximo),

corriente de carga: 2 o 3 x 800 mA.

ROBOT MÓVIL AUTÓNOMO TIPO DIFERENCIAL (https://roboticoss.com/curso/robotica-con-python-y-arduino-robot-movil-diferencial/) | PÁG 3
1 | Switch | Interruptor Switch Mediano Negro para el encendido y apagado del robot
2 | Resistencias 10kΩ | Utilizados para reducir el voltaje de 5V a 3.3V y para el monitoreo del voltaje de la batería.
1 | Resistencia 4.7kΩ | Utilizados para el monitoreo del voltaje de la batería.
1 | Resistencia 22kΩ | Utilizados para reducir el voltaje de 5V a 3.3V
10 | Cables de conexión macho-hembra | Para realizar las conexiones

ROBOT MÓVIL AUTÓNOMO TIPO DIFERENCIAL (https://roboticoss.com/curso/robotica-con-python-y-arduino-robot-movil-diferencial/) | PÁG 4
6 | Metros de alambre de timbre | Para realizar las conexiones
1 | Protoboard pequeño | Para montar el Arduino Nano y los otros componentes


1 | Estructura | Estructura disponible en el curso para impresión 3D.


2 | Llantas Amarillas | Las llantas de este tipo necesitan un acople impreso 3D para acoplarse al eje del motor de 4mm (Disponible para descargar)

ROBOT MÓVIL AUTÓNOMO TIPO DIFERENCIAL (https://roboticoss.com/curso/robotica-con-python-y-arduino-robot-movil-diferencial/) | PÁG 5


1 | Llanta loca o castor | Distancia de taladros de anclaje: 24 x 28 mm compatible con la estructura proporcionada en el curso.


1 | Metro de termoencogible 2mm | Para aislar los puntos de soldadura con cautín.


12 | Tornillos M3x10 con tuerca hilo fino y cabeza tipo estrella | 8 para soporte del motor, 4 para acoplar el motor al soporte
4 | Tornillos M4x70 con tuerca hilo fino y cabeza tipo estrella | Para soporte de la segunda plataforma
8 | Tornillos M3x25 con tuerca hilo fino y cabeza tipo estrella | 4 para driver del motor, 4 para el soporte de la rueda loca

ROBOT MÓVIL AUTÓNOMO TIPO DIFERENCIAL (https://roboticoss.com/curso/robotica-con-python-y-arduino-robot-movil-diferencial/) | PÁG 6
2. HERRAMIENTAS A EMPLEAR PARA LA CONSTRUCCIÓN DEL ROBOT
CANTIDAD | HERRAMIENTA | DESCRIPCIÓN | REFERENCIA
1 | Cautín | Herramienta para soldar los cables y componentes electrónicos
1 | Rollo de estaño | Rollo de soldadura para soldar los cables y componentes electrónicos
1 | Multímetro | Para medir continuidad, voltaje y corriente y así detectar posibles fallas.
1 | Destornillador estrella | Para los tornillos de la plataforma

ROBOT MÓVIL AUTÓNOMO TIPO DIFERENCIAL (https://roboticoss.com/curso/robotica-con-python-y-arduino-robot-movil-diferencial/) | PÁG 7
1 | Pistola de silicona | Para sujetar los elementos
10 | Barras de silicona | Barras grandes para pistola de silicona

ROBOT MÓVIL AUTÓNOMO TIPO DIFERENCIAL (https://roboticoss.com/curso/robotica-con-python-y-arduino-robot-movil-diferencial/) | PÁG 8
3. DISPOSITIVOS A UTILIZAR.
CANTIDAD | DISPOSITIVO | DESCRIPCIÓN
1 | Computador con Windows | En el curso se trabaja con el sistema operativo Windows (no abra soporte para otros sistemas operativos)

ROBOT MÓVIL AUTÓNOMO TIPO DIFERENCIAL (https://roboticoss.com/curso/robotica-con-python-y-arduino-robot-movil-diferencial/) | PÁG 9
4. SOTFWARE A EMPLEAR

¡NOTA! Verificar si el proceso de Instalación está incluido en el curso.

SOTFWARE | DESCRIPCIÓN | LINK DE DESCARGA | PROCESO DE INSTALACIÓN
Python 3.8.6 | Utilizado para la simulación y el desarrollo de controladores de nivel medio | https://www.python.org/ftp/python/3.8.6/python-3.8.6-amd64.exe (https://www.python.org/ftp/python/3.8.6/python-3.8.6-amd64.exe) | Incluido en el curso
Arduino 1.8.15 | Utilizado para programar los componentes de robot y control de nivel medio | https://www.arduino.cc/en/donate/ | No incluido en el curso
Sketchup 2019 | Utilizado para exportar el modelo CAD a Python | No incluido https://www.sketchup.com/es/products/sketchup-for-web (https://www.sketchup.com/es/products/sketchup-for-web) | No incluido en el curso

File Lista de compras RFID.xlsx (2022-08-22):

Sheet: 18 Kits
Robot diferencial
N | Cantidad | Descripción | Costo Unitario MXN | Costo Total | Referencia
1 | 18 | Modulo Lector RFID RC522 | 43.71 | 786.78 | https://uelectronics.com/producto/modulo-lector-rfid-rc522/
2 | 18 | ESP32 DEVKIT V1 30 Pines Wifi + Bluetooth | 147.27 | 2650.86 | https://uelectronics.com/producto/devkitv1-esp32-modulo-wifi-bluetooth-esp32-arduino/
3 | 18 | Cable USB | 24.6 | 442.8 | https://uelectronics.com/producto/cable-usb-a-microusb-1m-para-nodemcu-esp32-2/
4 | 18 | Mini protoboard |  | 0
5 | 23 | Servomotor SG90 RC 9g | 45 | 1035 | https://uelectronics.com/producto/servomotor-sg90-rc-9g/
6 | 72 | Leds |  | 0
7 | 72 | Resistencia de 100 Ohms |  | 0
8 | 216 | Jumpers M-M |  | 0
9 | 126 | Jumpers M-H |  | 0
10 | 6 | Gripper - impresión 3d |  | 0
11 |  |  |  | 0
12 |  |  |  | 0
 | 587 |  | Total | 4915.44

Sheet: Material Individual
Robot diferencial
N | Cantidad | Descripción | Costo Unitario MXN | Costo Total | Referencia
1 | 1 | Modulo Lector RFID RC522 | 43.71 | 43.71 | https://uelectronics.com/producto/modulo-lector-rfid-rc522/
2 | 1 | ESP32 DEVKIT V1 30 Pines Wifi + Bluetooth | 147.27 | 147.27 | https://uelectronics.com/producto/devkitv1-esp32-modulo-wifi-bluetooth-esp32-arduino/
3 | 1 | Cable USB | 24.6 | 24.6 | https://uelectronics.com/producto/cable-usb-a-microusb-1m-para-nodemcu-esp32-2/
4 | 1 | Mini protoboard |  | 0
5 | 1 | Servomotor SG90 RC 9g | 45 | 45 | https://uelectronics.com/producto/servomotor-sg90-rc-9g/
6 | 4 | Leds |  | 0
7 | 4 | Resistencia de 100 Ohms |  | 0
8 | 12 | Jumpers M-M |  | 0
9 | 7 | Jumpers M-H | 45 | 315
10 |  |  |  | 0
11 |  |  |  | 0
12 |  |  |  | 0
 | 32 |  | Total | 575.58

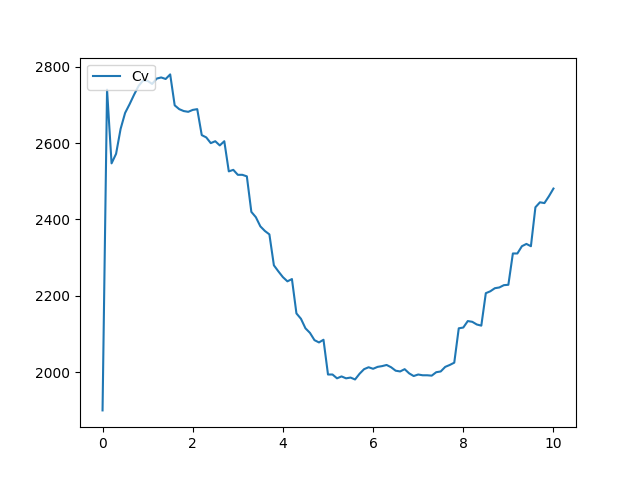
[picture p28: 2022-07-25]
Material support/SintonizacionLambdaCvInt.png

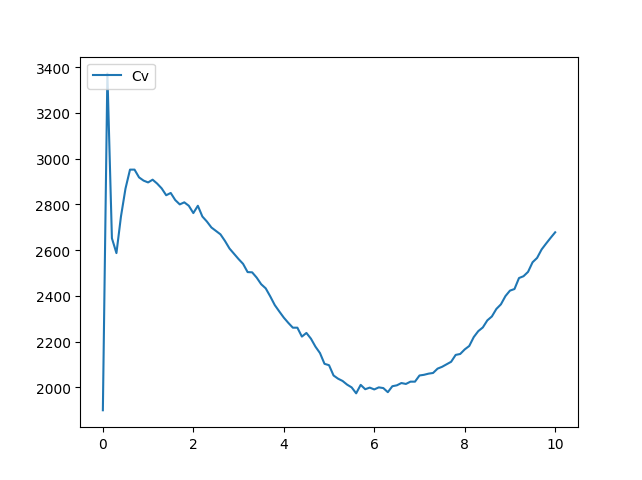
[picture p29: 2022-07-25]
Material support/SintonizacionFina05-Cv-P0.5.png

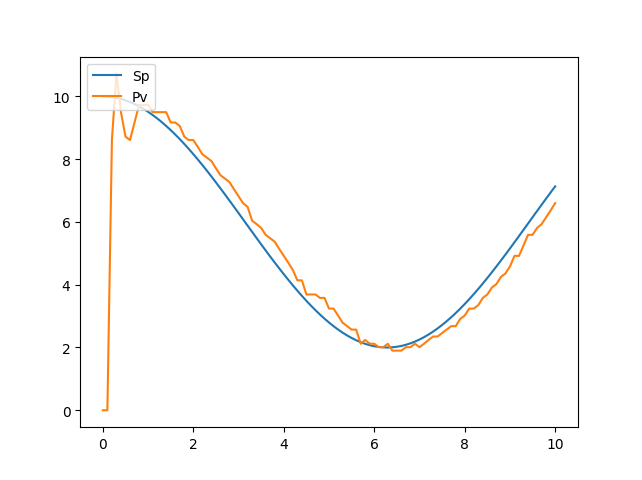
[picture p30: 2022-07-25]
Material support/SintonizacionFina05-Pv-P0.5.png

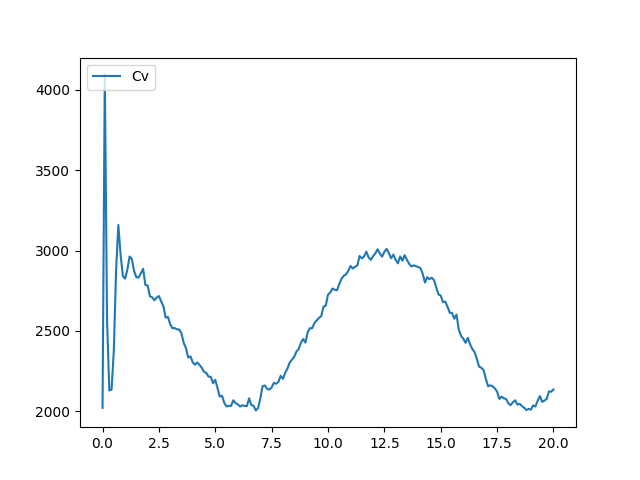
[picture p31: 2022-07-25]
Material support/SintonizacionFina08-Cv-Completa-RM.png

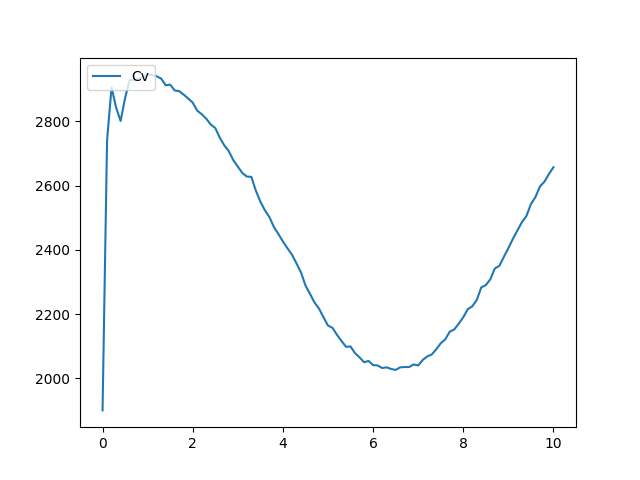
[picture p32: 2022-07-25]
Material support/SintonizacionFina01-Cv-I0.15.png

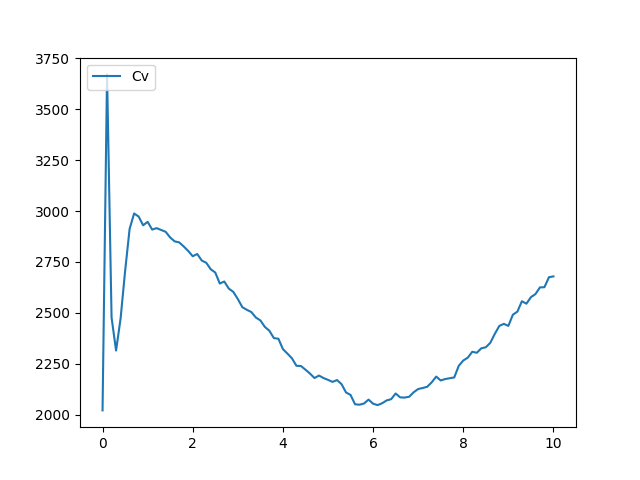
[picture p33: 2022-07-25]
Material support/SintonizacionFina03-Cv-P0.55.png

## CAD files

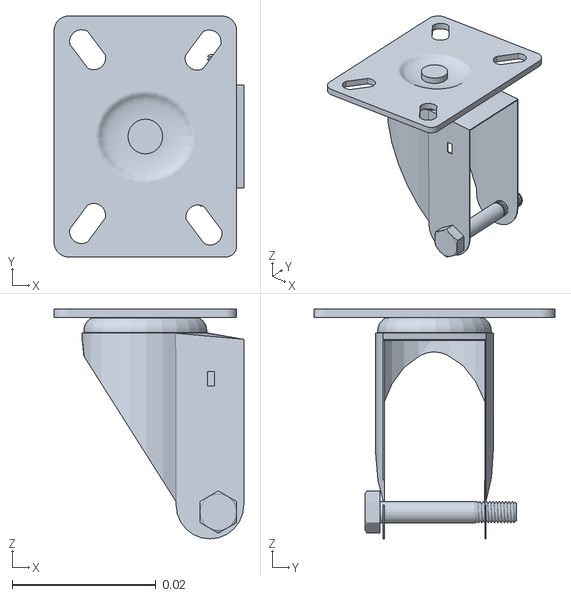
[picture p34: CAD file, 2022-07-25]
Material support/Documentation/3_Exportar_modelo_3D_a_Python/stl/4_BaseRuedaLoca.stl
0.0264 x 0.0335 x 0.032

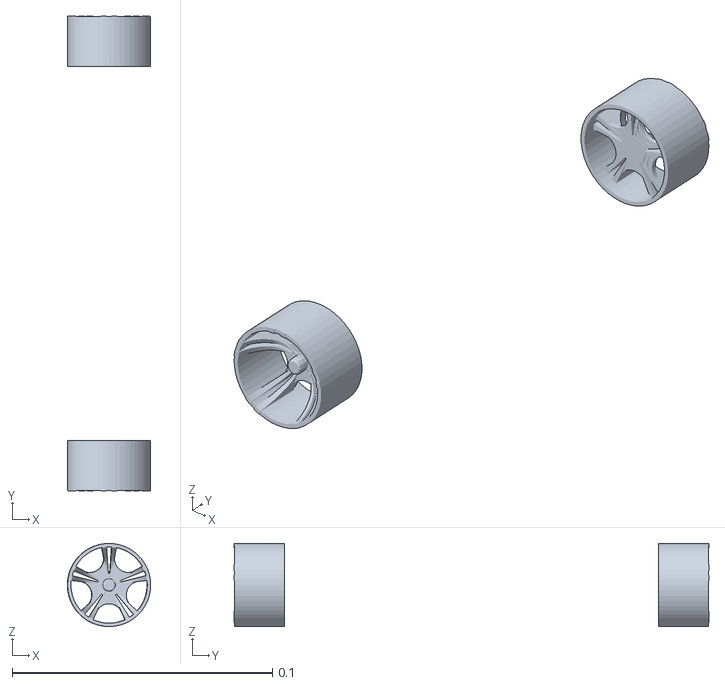
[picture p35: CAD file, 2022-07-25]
Material support/Documentation/3_Exportar_modelo_3D_a_Python/stl/1_BaseRueda.stl
0.0321 x 0.182 x 0.0319

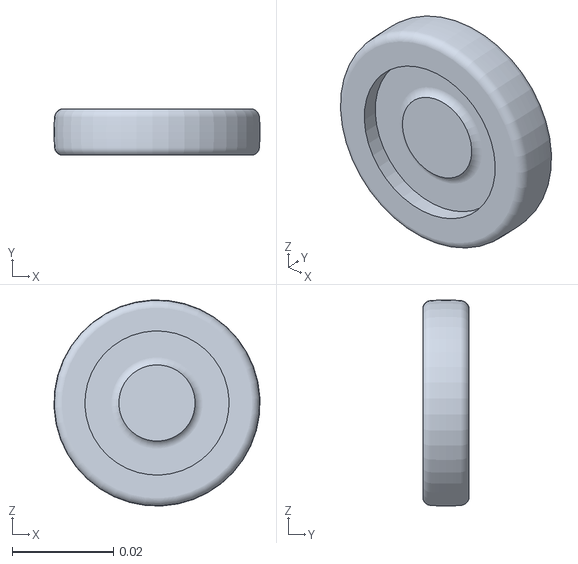
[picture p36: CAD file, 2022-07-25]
Material support/Documentation/3_Exportar_modelo_3D_a_Python/stl/5_RuedaLoca.stl
0.0406 x 0.00914 x 0.0406

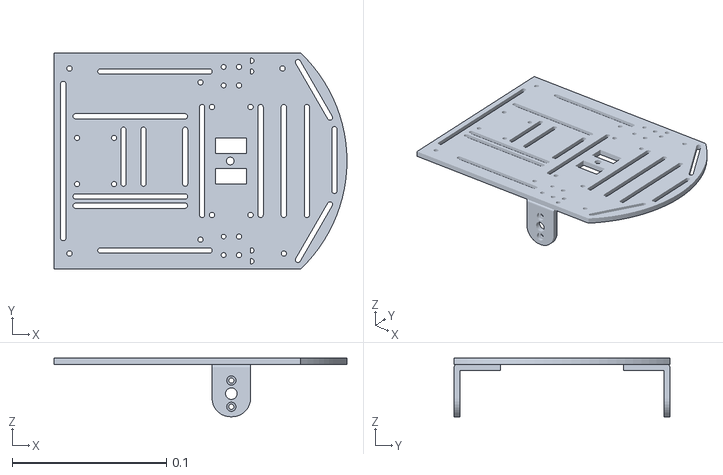
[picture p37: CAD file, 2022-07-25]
Material support/Documentation/3_Exportar_modelo_3D_a_Python/stl/6_Estructura.stl
0.19 x 0.14 x 0.038

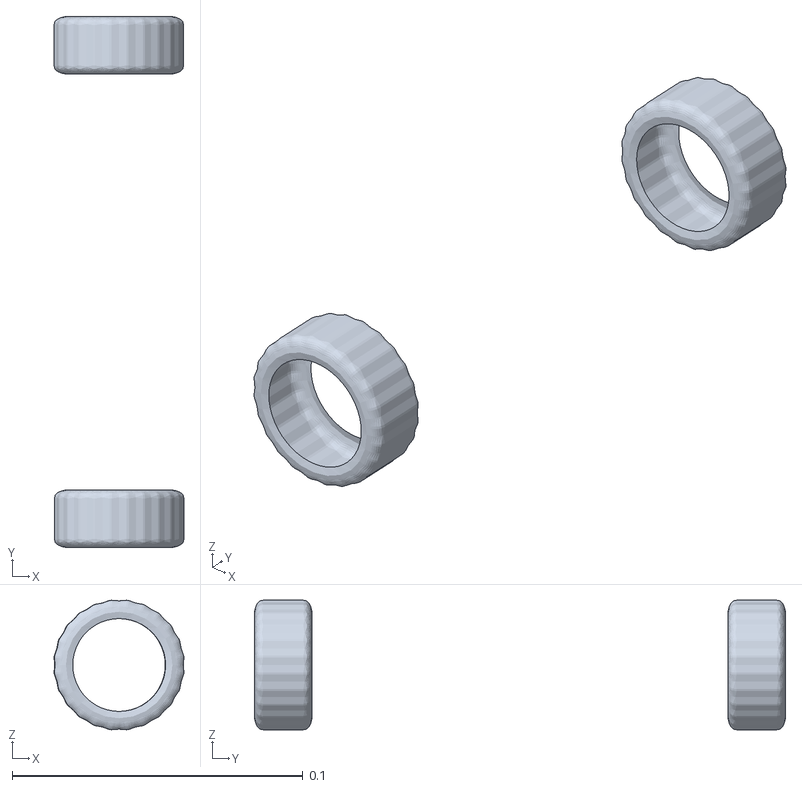
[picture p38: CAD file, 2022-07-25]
Material support/Documentation/3_Exportar_modelo_3D_a_Python/stl/2_Rueda.stl
0.0447 x 0.183 x 0.0446

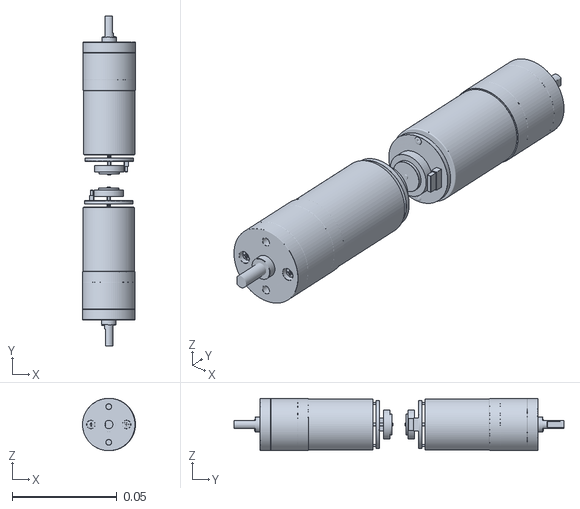
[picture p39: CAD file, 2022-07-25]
Material support/Documentation/3_Exportar_modelo_3D_a_Python/stl/3_Motores.stl
0.0252 x 0.157 x 0.025

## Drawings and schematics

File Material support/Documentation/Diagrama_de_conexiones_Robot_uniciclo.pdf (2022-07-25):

# Comunicación inalámbrica

# Alimentación

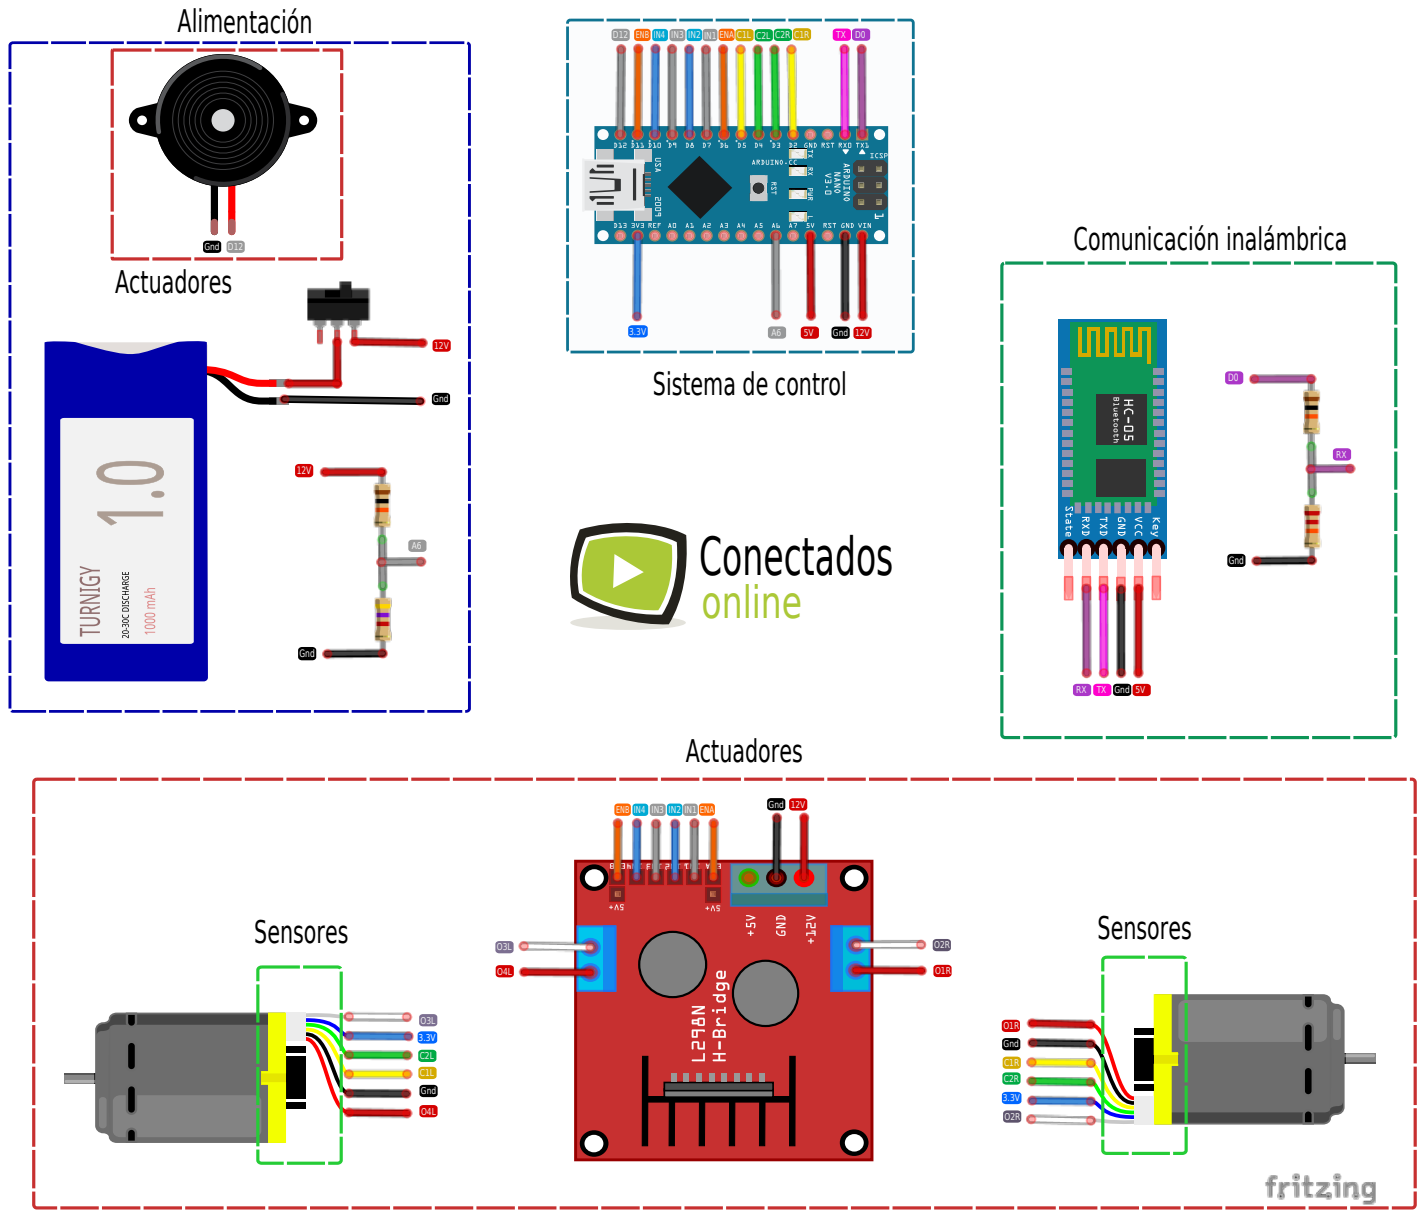
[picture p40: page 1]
Conectados online; Gnd; Gnd D12; Gnd 12V; D12 ENB IN4 IN3 IN2 IN1 ENA C1L C2L C2R C1R; ENB IN4 IN3 IN2 IN1 ENA; Actuadores; Sensores

Sistema de control

RX TX Gnd 5V

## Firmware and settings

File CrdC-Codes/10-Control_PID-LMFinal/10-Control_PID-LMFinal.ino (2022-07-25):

#include "motorControl.h"

#define EnML 15
#define ML_A 2
#define ML_B 4

#define MLenc_A 21 // Amarillo
#define MLenc_B 19 // Blanco

// Configurando los parámetros de PWM
const int frecuencia = 10000;
const int canal_L = 0;
const int resolucion = 12;

volatile long L_pulses = 0;
volatile long CurrentPulsesL = 0;

double wRef = 0.0;        // Velocidad angular en rad/s
double w = 0.0;           // Velocidad angular de referencia en rad/s

const double constValue = 11.18;
//const double constValue = 0.3913;
int cv = 0;

unsigned long lastTime = 0; // Tiempo anterior
unsigned long sampleTime = 100; // Tiempo de muestreo
unsigned int R = 562; // Resolucion del encoder R = mH*s*r

String inputString = "";
bool stringComplete = false;
const char separator = ',';
const int datoLength = 1;
double dato[datoLength];

motorControl motor(sampleTime);

//--------------setup------------
void setup() {
  pinMode(EnML, OUTPUT);
  pinMode(ML_A, OUTPUT);
  pinMode(ML_B, OUTPUT);
  
  pinMode(MLenc_A, INPUT);    
  pinMode(MLenc_B, INPUT);

  ledcSetup(canal_L, frecuencia, resolucion);

  ledcAttachPin(EnML, canal_L);
  
  attachInterrupt(MLenc_A, encoderL, RISING);

  Serial.begin(115200);

  //motor.lambdaTunning(1.1408,0.1032,0.0896);   // const de porporcionalidad, const de tiempo en lazo abierto,retardo
  motor.setGains(0.5, 0.04, 0.04);
  
  motor.setCvLimits(4095,1900);               // valores límites de pwm, para vel máxima y minima
  motor.setPvLimits(19,0);                    // valores límites en rad/s
  
//  Serial.print(motor.getK());
//  Serial.print(", ");
//  Serial.print(motor.getTi());
//  Serial.print(", ");
// Serial.println(motor.getTd());
  lastTime = millis();
}


//--------------loop------------
void loop() {
  if (stringComplete) {
    for (int i = 0; i < datoLength; i++){
      int index = inputString.indexOf(separator);
      dato[i] = inputString.substring(0,index).toFloat();
      inputString = inputString.substring(index+1);
    }
    wRef = dato[0];
    
    inputString = ""; 
    stringComplete = false; 
  }
  
  velValue();
  
}


//--------------functions------------
void serialEvent(){
  while (Serial.available()) {
    char inChar = (char)Serial.read();
    inputString += inChar; 
    if (inChar == '\n') {
      stringComplete = true; 
    } 
  }
}

void velValue(){
  if (millis() - lastTime >= sampleTime){ // Se actualiza cada sampleTime (milisegundos)
    
    
    w =(constValue*L_pulses)/((millis()-lastTime));// Velocidad en RPM
    lastTime = millis();            // Almacenamos el tiempo actual
    L_pulses = 0;                   // Reiniciamos los pulsos
    
    cv = motor.compute(wRef,w);           // Control PID
    
    if (cv > 1){
      clockwise (cv);
    }
    else if (cv < 1){
      anticlockwise(abs(cv));
    }
    else{
      anticlockwise (0);
    }
    
    Serial.println(w);
    Serial.println(cv);
  }
}

void encoderL(){
  if (digitalRead(MLenc_B) == HIGH){     // si B es HIGH, sentido horario
    L_pulses++ ;        // incrementa POSICION en 1
  }
  else {          // si B es LOW, sentido anti horario
    L_pulses-- ;        // decrementa POSICION en 1
  }

  CurrentPulsesL = L_pulses;
}

void clockwise(int vel){
  digitalWrite(ML_A, LOW);
  digitalWrite(ML_B, HIGH);
  ledcWrite(canal_L, vel);
  if (vel < 1) {
    digitalWrite(ML_A, LOW);
    digitalWrite(ML_B, LOW);
    ledcWrite(canal_L, 0);
  }
}

void anticlockwise(int vel){
  digitalWrite(ML_A, HIGH);
  digitalWrite(ML_B, LOW);
  ledcWrite(canal_L, vel);
  if (vel < 1) {
    digitalWrite(ML_A, LOW);
    digitalWrite(ML_B, LOW);
    ledcWrite(canal_L, 0);
  }
}

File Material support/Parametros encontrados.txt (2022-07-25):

kp = 1.1408
tau = 0.1032
delay = 0.0896

Datos recibido cuando se hace sintonia con Lamda
0.37, 0.15, 0.03

SintonizacionLambdaFloat

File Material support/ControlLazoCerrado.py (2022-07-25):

from pyArduino import *
import matplotlib.pyplot as plt
#import numpy as np

ts = 0.1 # Tiempo de muestreo
tf = 20 # Tiempo de simulacion
t = np.arange(0,tf+ts,ts) # Array de tiempo
N = len(t) # Numero de muestras

######################## Comunicacion Serial ###############

port = 'COM10'  # Com ESP32
baudRate = 115200 # Velocidad de transmisión en Baudios de la ESP32

arduino = serialArduino(port,baudRate,2)# Objeto serial

arduino.readSerialStart() # Inicia lectura de datos

######################### Señales #####################

pv  = np.zeros(N) # Variable de proceso (Pv) - Donde se almacenará la lectura de la velocidad en rad/s
cv  = np.zeros(N) # Variable de control (Cv)
sp = np.zeros(N) # Variable de deseada (Sp) - Set point

######################### Setpoint Escalon ################
##Inicialmente será un escalón de cero y después se convierte en un escalón de 8 rad/s
""" for k in range(N):
     if k*ts > 3:
          sp[k] = 8    
     else:
          sp[k] = 0  """
          
###################### Setpoint Trayectoria ################
sp = 4*np.cos(0.5*t)+6

########################## Loop ########################

for k in range(N):

     start_time = time.time() # Tiempo actual
     
     arduino.sendData([sp[k]]) # Enviar Sp (debe ser una lista)
     
     pv[k] = arduino.rawData[0] # Recibir Pv 
     cv[k] = arduino.rawData[1] # Recibir Cv
     
     elapsed_time = time.time() - start_time # Tiempo transcurrido
     
     time.sleep(ts-elapsed_time) # Esperar hasta completar el tiempo de muestreo
     
     
arduino.sendData([0]) # Detener motor     
arduino.close() # Cerrar puerto serial
     
###################### Mostrar figuras ######################
plt.figure()     
plt.plot(t,sp,label='Sp')     
plt.plot(t,pv,label='Pv')
plt.legend(loc='upper left')

plt.figure() 
plt.plot(t,cv,label='Cv')
plt.legend(loc='upper left')

plt.show()

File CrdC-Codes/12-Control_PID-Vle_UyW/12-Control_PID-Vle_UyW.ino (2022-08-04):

#include "BluetoothSerial.h"

#if !defined(CONFIG_BT_ENABLED) || !defined(CONFIG_BLUEDROID_ENABLED)
#error Bluetooth is not enabled! Please run `make menuconfig` to and enable it
#endif

BluetoothSerial SerialBT;

#include "motorControl.h"

#define EnML 15
#define ML_A 2
#define ML_B 4

#define EnMR 5
#define MR_A 16
#define MR_B 17

#define MLenc_A 21 // Amarillo
#define MLenc_B 19 // Blanco

#define MRenc_A 22 // Amarillo
#define MRenc_B 23 // Blanco

// Configurando los parámetros de PWM
const int frecuencia = 10000;
const int canal_L = 0;
const int canal_R = 1;
const int resolucion = 12;

volatile long L_pulses = 0;

volatile long R_pulses = 0;

double wLRef = 0.0;        // Velocidad angular en rad/s
double wL = 0.0;           // Velocidad angular de referencia en rad/s

double wRRef = 0.0;        // Velocidad angular en rad/s
double wR = 0.0;           // Velocidad angular de referencia en rad/s

const double constValue = 11.18;      
const double radio = 0.035;         // radio en metros
const double L = 0.175;             // Distancia entre llanta en metros
double uRobot = 0;                  // Velocidad lineal del robot
double wRobot = 0;                  // Velocidad angular del robot
double phi = 0;                     // Angulo del robot respecto a la referencia

//const double constValue = 0.3913;

int cvL = 0;
int cvR = 0;

unsigned long lastTime = 0; // Tiempo anterior
unsigned long sampleTime = 100; // Tiempo de muestreo
unsigned int R = 562; // Resolucion del encoder R = mH*s*r

String inputString = "";
bool stringComplete = false;
const char separator = ',';
const int datoLength = 2;
double dato[datoLength];

motorControl motorL(sampleTime);
motorControl motorR(sampleTime);


//--------------setup------------
void setup() {
  pinMode(EnML, OUTPUT);
  pinMode(ML_A, OUTPUT);
  pinMode(ML_B, OUTPUT);

  pinMode(EnMR, OUTPUT);
  pinMode(MR_A, OUTPUT);
  pinMode(MR_B, OUTPUT);
  
  pinMode(MLenc_A, INPUT);    
  pinMode(MLenc_B, INPUT);

  pinMode(MRenc_A, INPUT);    
  pinMode(MRenc_B, INPUT);

  ledcSetup(canal_L, frecuencia, resolucion);
  ledcSetup(canal_R, frecuencia, resolucion);

  ledcAttachPin(EnML, canal_L);
  ledcAttachPin(EnMR, canal_R);
  
  attachInterrupt(MLenc_A, encoderL, RISING);
  attachInterrupt(MRenc_A, encoderR, RISING);

  Serial.begin(115200);
  SerialBT.begin("ColmiBot"); //Bluetooth device name

  motorL.setGains(0.45, 0.04, 0.04);           //K, Ti, Td
  motorR.setGains(0.45, 0.04, 0.04);           //K, Ti, Td
  
  motorL.setCvLimits(4095,1900);               // valores límites de pwm, para vel máxima y minima
  motorL.setPvLimits(19,0);                    // valores límites en rad/s

  motorR.setCvLimits(4095,1900);               // valores límites de pwm, para vel máxima y minima
  motorR.setPvLimits(19,0);                    // valores límites en rad/s

  lastTime = millis();
}


//--------------loop------------
void loop() {
  if (stringComplete) {
    for (int i = 0; i < datoLength; i++){
      int index = inputString.indexOf(separator);
      dato[i] = inputString.substring(0,index).toFloat();
      inputString = inputString.substring(index + 1);
    }

    velocityMotor(dato[0],dato[1]);     // Velocidad lineal del robot y angular
    
    inputString = ""; 
    stringComplete = false; 
  }
  
  velValue();
  serialEventBT();
}


//--------------functions------------
void serialEvent(){
  while (Serial.available()) {
    char inChar = (char)Serial.read();
    inputString += inChar; 
    if (inChar == '\n') {
      stringComplete = true; 
    } 
  }
}

void serialEventBT(){
  while (SerialBT.available()) {
    char inChar = (char)SerialBT.read();
    inputString += inChar; 
    if (inChar == '\n') {
      stringComplete = true; 
    } 
  }
}

void velValue(){
  if (millis() - lastTime >= sampleTime){ // Se actualiza cada sampleTime (milisegundos)
    
    wL =(constValue*L_pulses)/((millis()-lastTime));// Velocidad en RPM
    wR =(constValue*R_pulses)/((millis()-lastTime));// Velocidad en RPM
    
    lastTime = millis();            // Almacenamos el tiempo actual
    
    L_pulses = 0;                   // Reiniciamos los pulsos
    R_pulses = 0;                   // Reiniciamos los pulsos
    
    cvL = motorL.compute(wLRef,wL);           // Control PID
    cvR = motorR.compute(wRRef,wR);           // Control PID
    
    if (cvL > 1) clockwiseL (cvL);
    else if (cvL < 1) anticlockwiseL(abs(cvL));
    else anticlockwiseL (0);

    if (cvR > 1) clockwiseR (cvR);
    else if (cvR < 1) anticlockwiseR(abs(cvR));
    else anticlockwiseR (0);

    velocityRobot(wL,wR);
    
    Serial.println(uRobot);
    Serial.println(wRobot);
    //Serial.println(phi);

    SerialBT.print(uRobot);
    SerialBT.print("  ");
    SerialBT.println(wRobot);
    //SerialBT.println(phi);
    
  }
}

void encoderL(){
  if (digitalRead(MLenc_B) == HIGH){     // si B es HIGH, sentido horario
    L_pulses++ ;        // incrementa POSICION en 1
  }
  else {          // si B es LOW, sentido anti horario
    L_pulses-- ;        // decrementa POSICION en 1
  }

}

void encoderR(){
  if (digitalRead(MRenc_B) == HIGH){     // si B es HIGH, sentido horario
    R_pulses-- ;        // incrementa POSICION en 1
  }
  else {          // si B es LOW, sentido anti horario
    R_pulses++ ;        // decrementa POSICION en 1
  }

}

void clockwiseL(int vel){
  digitalWrite(ML_A, LOW);
  digitalWrite(ML_B, HIGH);
  ledcWrite(canal_L, vel);
  if (vel < 1) {
    digitalWrite(ML_A, LOW);
    digitalWrite(ML_B, LOW);
    ledcWrite(canal_L, 0);
  }
}

void anticlockwiseL(int vel){
  digitalWrite(ML_A, HIGH);
  digitalWrite(ML_B, LOW);
  ledcWrite(canal_L, vel);
  if (vel < 1) {
    digitalWrite(ML_A, LOW);
    digitalWrite(ML_B, LOW);
    ledcWrite(canal_L, 0);
  }
}

void clockwiseR(int vel){
  digitalWrite(MR_A, LOW);
  digitalWrite(MR_B, HIGH);
  ledcWrite(canal_R, vel);
  if (vel < 1) {
    digitalWrite(MR_A, LOW);
    digitalWrite(MR_B, LOW);
    ledcWrite(canal_R, 0);
  }
}

void anticlockwiseR(int vel){
  digitalWrite(MR_A, HIGH);
  digitalWrite(MR_B, LOW);
  ledcWrite(canal_R, vel);
  if (vel < 1) {
    digitalWrite(MR_A, LOW);
    digitalWrite(MR_B, LOW);
    ledcWrite(canal_R, 0);
  }
}

void velocityMotor(double u, double w){
  wLRef = (u - (L*w/2))/radio;
  wRRef = (u + (L*w/2))/radio;
}

void velocityRobot(double wL, double wR){
  uRobot = (radio *(wR + wL)) / 2;     //Promedio de las velocidades angulares por el radio de la llanta
  wRobot = (radio *(wR - wL)) / L;     //Diferencia entre las velocidades angulares por el radio de la llanta entre la distancia entre ellas
  phi = phi + sampleTime * wRobot;
}

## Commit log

2022-07-20 Material que descargué para el entendimiento de lo que se está realizando
2022-07-20 Código que se ha realizado paso a paso desde la lectura de un encoder para mover y leer la posición, velocidad angular y lineal de un motor
2022-07-20 Decodificación de los 10 dígitos de las tarjetas disponibles
2022-07-20 Se establecio el valor de PWM mínimo donde la rueda con fricción, rodara
2022-07-20 Se modificó el valor mínimo de tal forma que al ingresar pasar valor 0 como control value, se detuviera el motor
2022-07-20 Se realizó la prueba del código de Control por lazo abierto y se obtuvieron las gráficas de comportamiento de la velocidad del robot ante un etrada escalón del 40%, lo que permitió obtener el kp para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
    [Parametros encontrados.txt]
2022-07-20 Programa de control PID donde se ingresaron los parametros kp, tau y delay
2022-07-25 Documento donde se describe a los alumnos lo que deberán realizar en el proyecto
2022-07-25 Archivo donde se explcia la sintonizacion de las constates del control PID
2022-07-25 Graficas del comportamineto del control ante la sintonizacion de diferentes valores de las constantes PID, en las ultimas se están modificando los valores de ki kp y kd de tal forma que el control te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
    [Parametros encontrados.txt]
2022-07-25 Sintonizacion de las constantes Kp y Ki
2022-07-25 Control del motor derecho sintonizado
2022-07-25 Control del motor Izquierdo sintonizado
2022-07-25 Control del robot, lo cual implica el control de ambos motores
2022-07-25 Control de los dos motores dl robot de forma inalambrica
2022-07-25 Diagrama de conexiones sugerido y bilbioteca para utilizar otros pines como interrupciones
2022-07-25 Mas graficas de las pruebas lo que llevó a tener los valoresfinales de las constantes de controlador PID
2022-07-25 Graficas que llevaron a los valores finales de la sintonizacion del controlador PID
2022-07-25 Elliminacion por error en el nombre
2022-07-25 Ahora se le pasan por serial dos parametros, la velocidad angular y después la velocidad angular
2022-07-25 Carpeta donde están los archivo stl y el programa para poder generar la simulacion, actualmente no funciona, se debe checar que es
    [1_BaseRueda.stl, 2_Rueda.stl, 3_Motores.stl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]
2022-07-25 Imagenes donde se describen las formulas para calcular la velocidad lineal y angular del robot con base en las velocidades de cada llanta
2022-07-26 Codigo en desarrollo para el control de la posición
2022-08-04 Codigo del proyecto de intro a ingenieria
2022-08-04 Codigo ejemplo para lectura de RFID
2022-08-22 Carta que se les dará a los alumnos para que se comprometan a devolver el material
2022-09-19 Cartas compromiso
    [I2C.fzz, RFID.fzz]
2022-09-19 Presentaciones de clase
